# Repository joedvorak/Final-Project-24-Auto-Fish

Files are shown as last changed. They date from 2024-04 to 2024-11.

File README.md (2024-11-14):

# BAE305 Final Project: Automatic Fish Tank Feeder
***BAE305 Final Project***
* Eli Barrow
* Alexis Puckett
* Hannah Markwell

## Summary:

Our BAE305 project is for an aquarium monitoring and feeding system. The system includes an automatic feeder that is on a timer for periods of 6 hours, 12 hours, and 24 hours, and it distributes food directly to the fish in the tank. The feeder uses an auger and stepper motor to push the fish food out of the container, into the fish tank. Our project also includes a mechanism that reads the temperature, displays it, and then turns on a red LED if the temperature falls below a specified point, and a green LED if the temperature is good for the safety of the fish. It also includes a feature that monitors the water level of the fish tank, and this feature turns on an LED to alert low water levels in the tank. Our display system displays the red and green LEDs for both the temperature and water level monitoring systems. It also has two screens, one to show the temperature and water level data, and one to show how much time is left until the next feeding. We used a potentiometer for the user to change the feeding time from 6, 12, and 24 hours. Finally, our display has two potentiometers to control the contrast of the screens. Both the feeder and display mechanical systems are 3D printed.

[Project Video Description: (https://www.youtube.com/shorts/zOCTcbQEuwI)](https://www.youtube.com/shorts/zOCTcbQEuwI)

## Design Description

### Materials:
 
For this project the materials needed are simple electrical components as well as the ability to access a 3D printer to print the larger mechanical parts of the system.
 The electrical components needed are:
 - 2 Arduino Uno Boards with Breadboards
 - Ability to connect the Uno to your computer
 - Approx. 50 wires that're compatible with the Arduino, Breadboard, and components
 - 2 LCD Screens
 - 1 5V DC Stepper Motor (ROHS 28byj-48)
 - 3 Potentiometers
 - 2 Push buttons
 - 2 Green LEDs
 - 2 Red LEDs
 - 1 Float Switch
 - 1 Thermistor
 - 6 1kOhm Resistors 
 - 1 10kOhm Precision Resistor (for thermistor)
 - 1 10 kOhm Resistor

 ### Physical Design: 

The design of the feeding system was a small hopper with an auger in the bottom of it that would be turned by a stepper motor to slowly push the food out of the front of the hopper body. There is a hole that runs from the back of the hopper body to the front of the hopper body where the auger slides into, with a stop being placed on the front side that does not allow the auger to slide all the way through. Below this stop is the funnel shape that the food will slide down into the tank to reach the fish. The base of the auger is specially designed to allow the shaft of the stepper motor to mate into the auger, connecting the two for a smooth rotational motion. The stepper motor came with a screw mounting bracket on each side, we then measured the size of those holes with calipers then created two extrusions on the back side of the hopper that would be used to mount the stepper motor. Then finally for a flush fit of the auger with the back wall of the hopper body some spacers were needed to be put on the shaft to create the proper offset of the stepper motor. The type of food that is normally given to the fish is very small spherical pellets that would almost flow fluidly in a system like this, so this design is what the team moved forward with. There was also a need for the hopper to be mounted to the back glass of the fish tank since there is no spot for the hopper to sit on top of the lid, so the team designed a bracket that mounts to the back glass of the tank for the hopper/feeding system to sit on. The design drawings of the Hopper, Bracket, Auger, and Spacers are shown below, as well as links to the online design file through OnShape, where the .stl files can be exported for 3D printing purposes.

<p align="center">
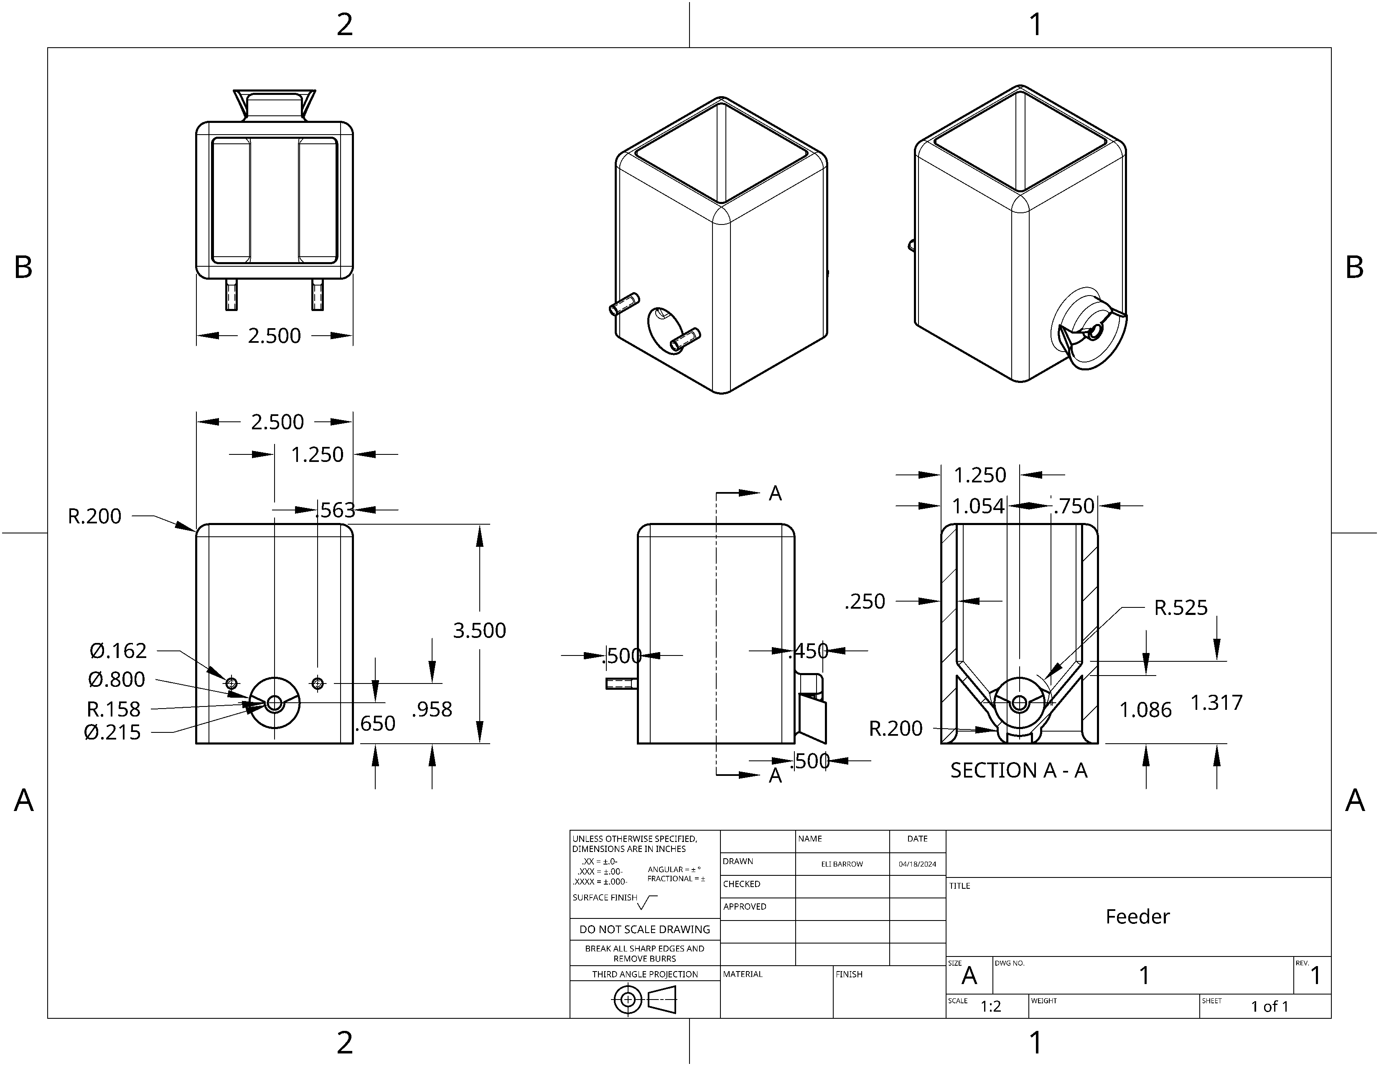
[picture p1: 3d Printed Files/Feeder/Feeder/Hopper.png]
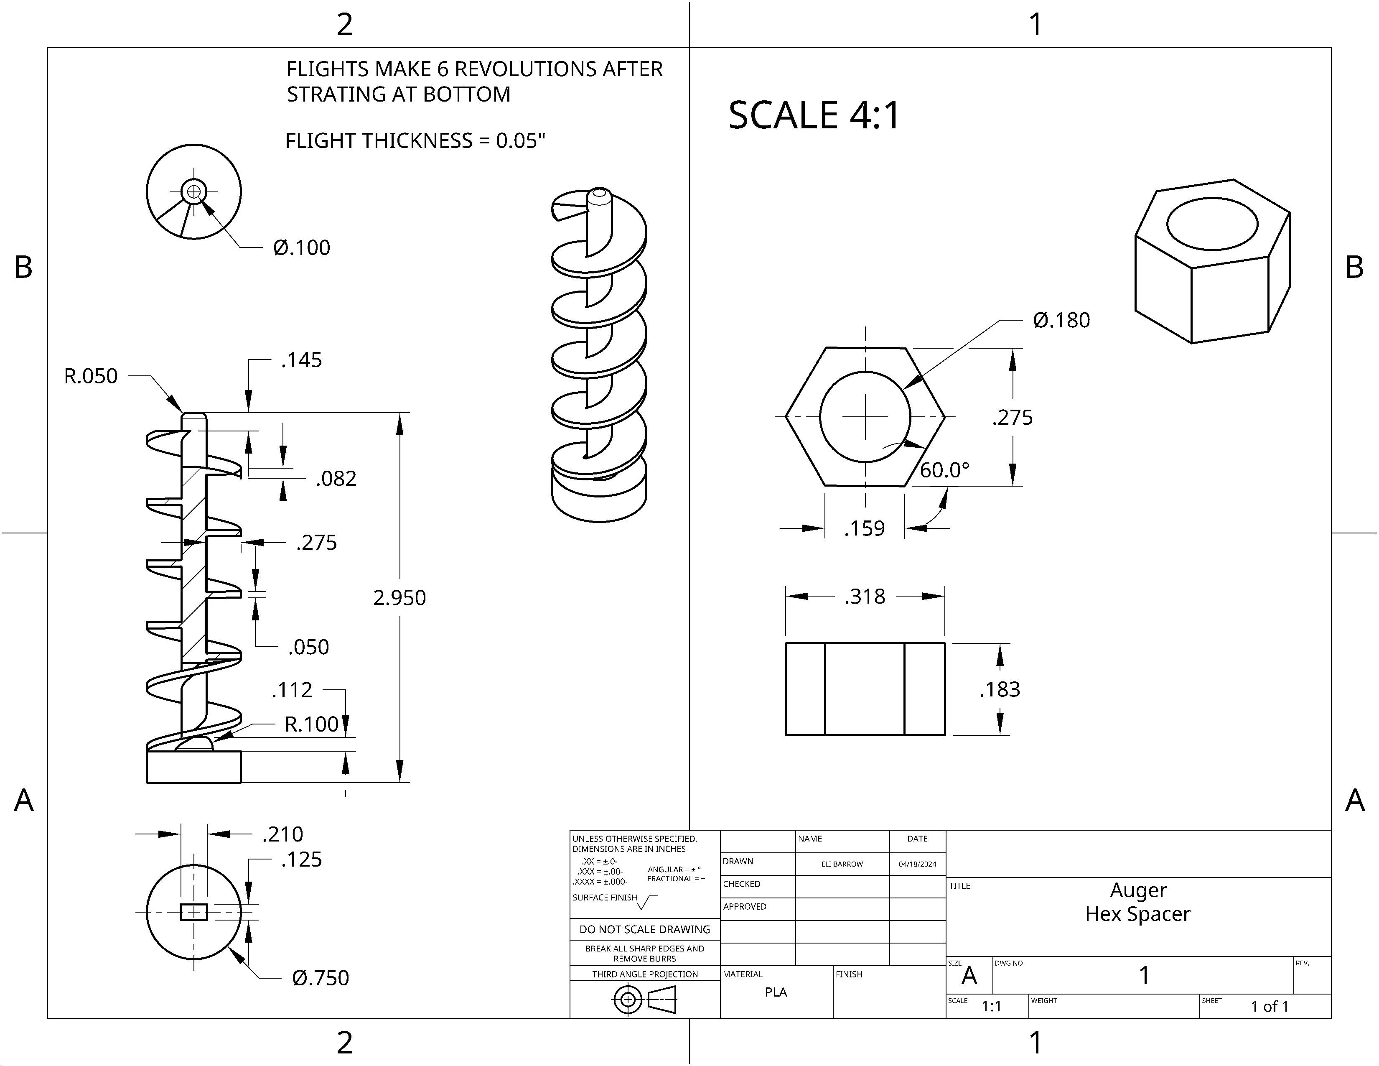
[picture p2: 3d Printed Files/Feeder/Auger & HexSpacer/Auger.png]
  
</p>

<p align="center">
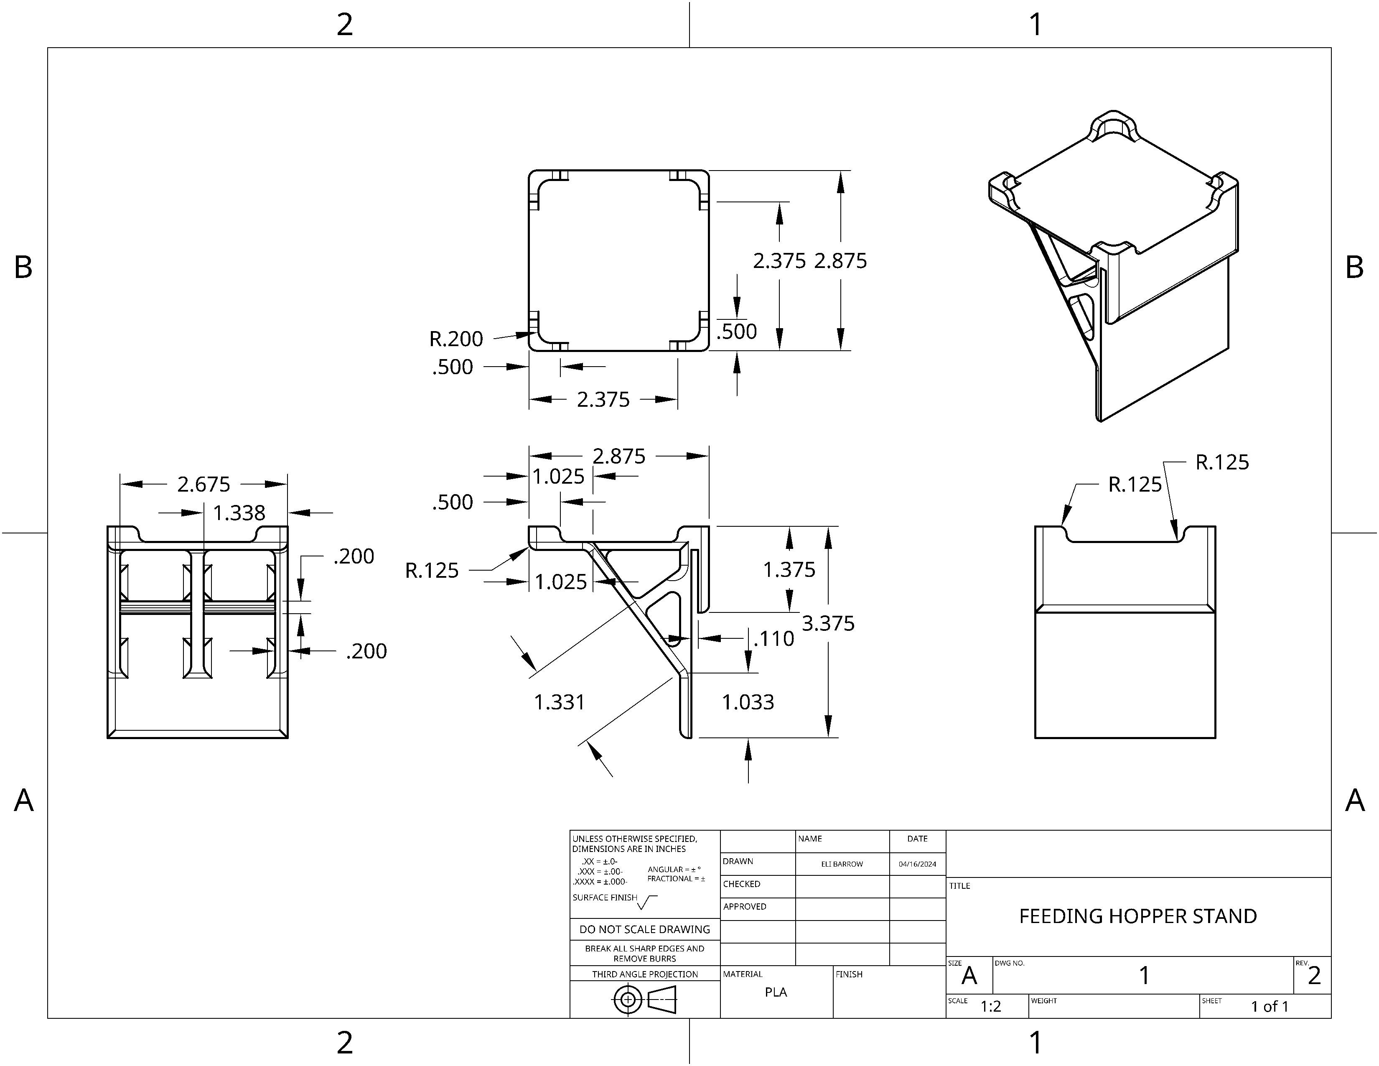
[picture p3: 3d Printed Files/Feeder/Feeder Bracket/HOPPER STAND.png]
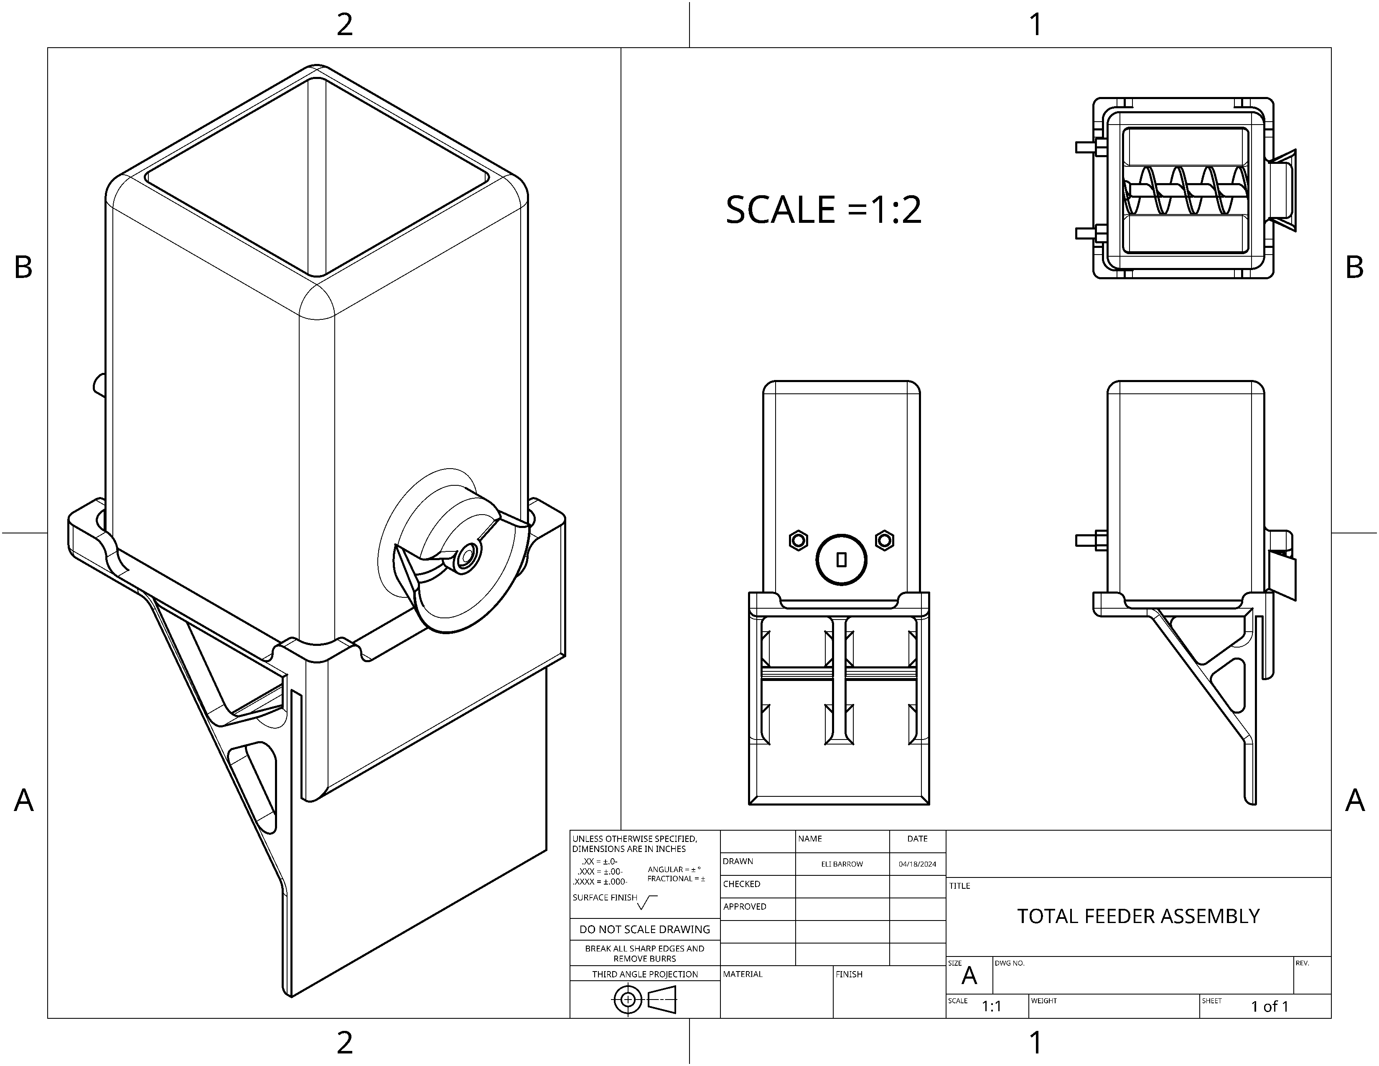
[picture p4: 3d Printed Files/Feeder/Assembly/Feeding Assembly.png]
  
</p>

**Link for Onshape Feeder Files:**
https://cad.onshape.com/documents/4df08dd93363a5b6d688b396/w/b2cb09403d87c3bcf0b51dba/e/0a122a04bef23e0f82b38aa6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

 After designing the Feeding system there was also a need to mount the thermistor and float switch to the back glass of the fish tank alongside the feeder. This only needed a few measurements taken of the float switch diameter and thermistor wire diameter to make a simple bracket, similar to the hopper bracket. The drawing file is shown below and is accompanied with a link to OnShape.

<p align="center">
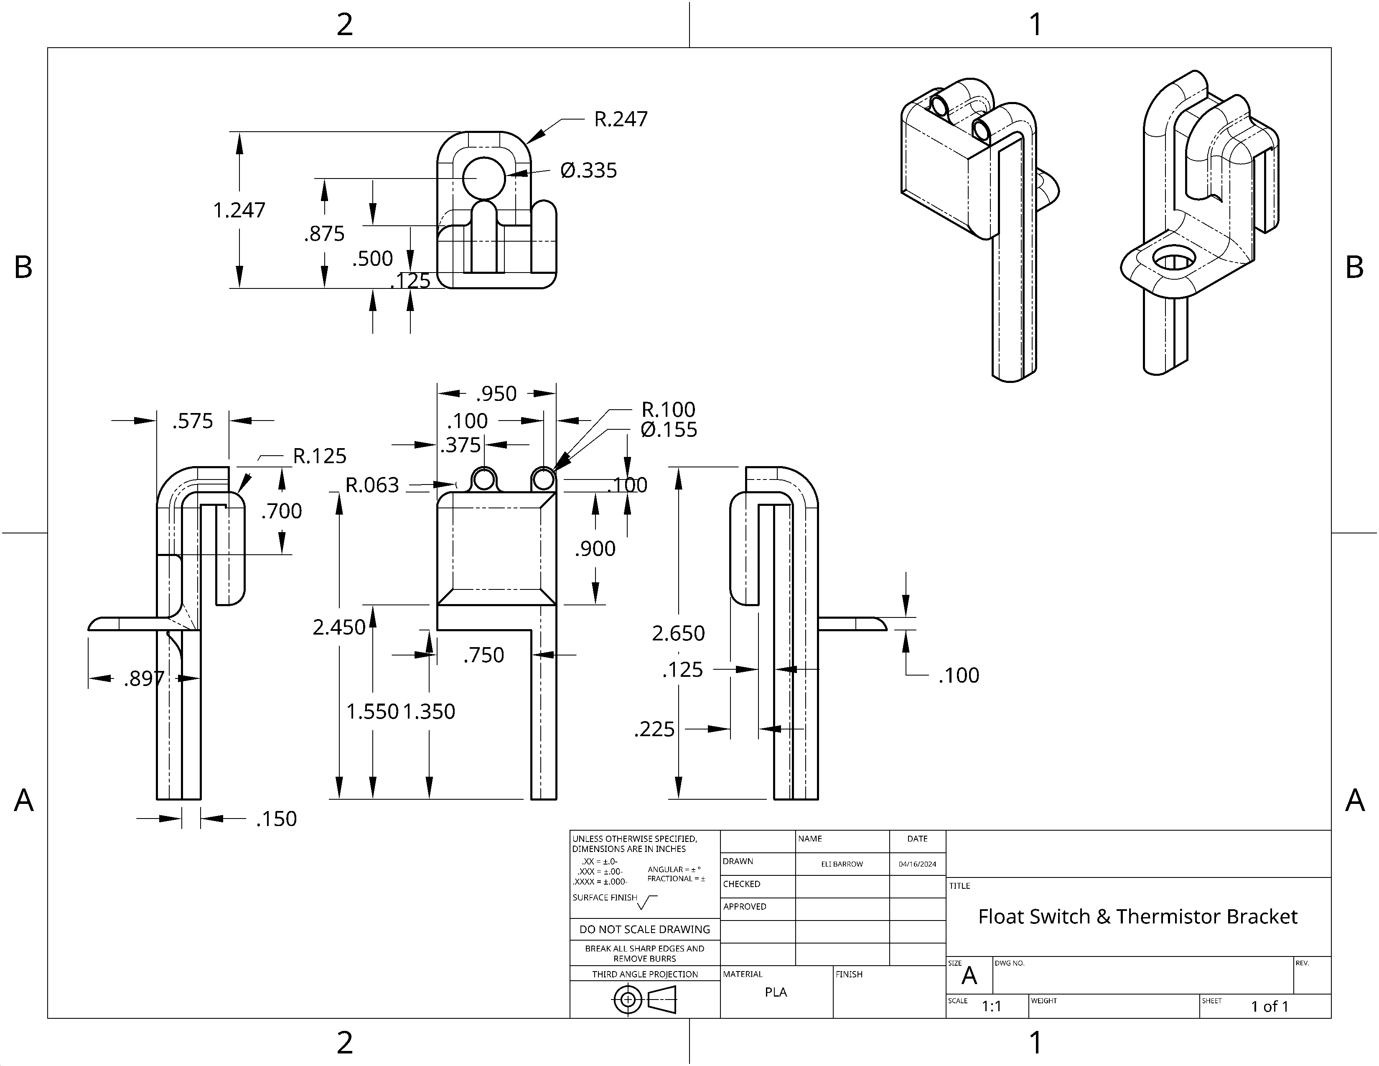
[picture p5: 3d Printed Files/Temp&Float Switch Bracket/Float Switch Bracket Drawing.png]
  
</p>

**Link for Onshape Float Switch & Thermistor Bracket Files:**   
https://cad.onshape.com/documents/ca7b3c8a11bfe362b02dd540/w/57267339f03928a64975b33e/e/b6ae37b48c85a3c1fea425d9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

**Picture of Assembly on Tank with Hopper and Float Switch Bracket:**
<p align="center">
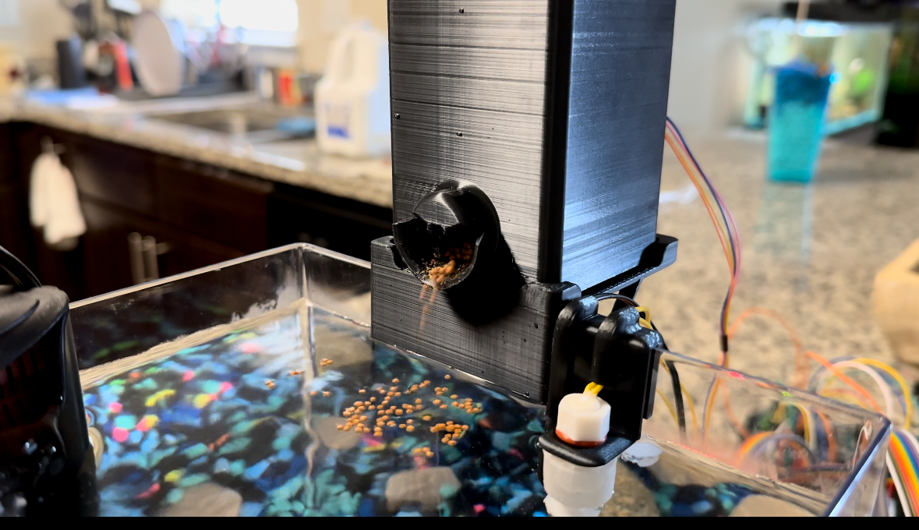
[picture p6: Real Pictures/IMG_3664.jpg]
  
</p>

Once the measurement tools and feeding systems were designed the only piece remaining was a panel for the user to control the system with. The group had previously put together the circuits for the project and had previously known that we need positions for a selecting button, reset button, a potentiometer for choosing the time interval, spaces for 4 LEDs, 2 spaces for LCD screens and finally 2 more potentiometers for controlling the contrast of the screens. The group measured the dimensions of the electrical components with calipers and put together the following control panel that will be used to control the system. The control panel also was in need of a back plate that could be removed that would allow someone to connect wires to the electrical components. There was also a need for braces that would keep the LCD screens in place to assure that they would be flush with the front surface of the control panel for a smooth exterior look. The tolerances were tight enough for the smaller components, so they did not need braces to be held into place. The drawing file of the control panel, back plate, internal braces, and assembly drawing is shown below and is accompanied with a link to OnShape.

<p align="center">
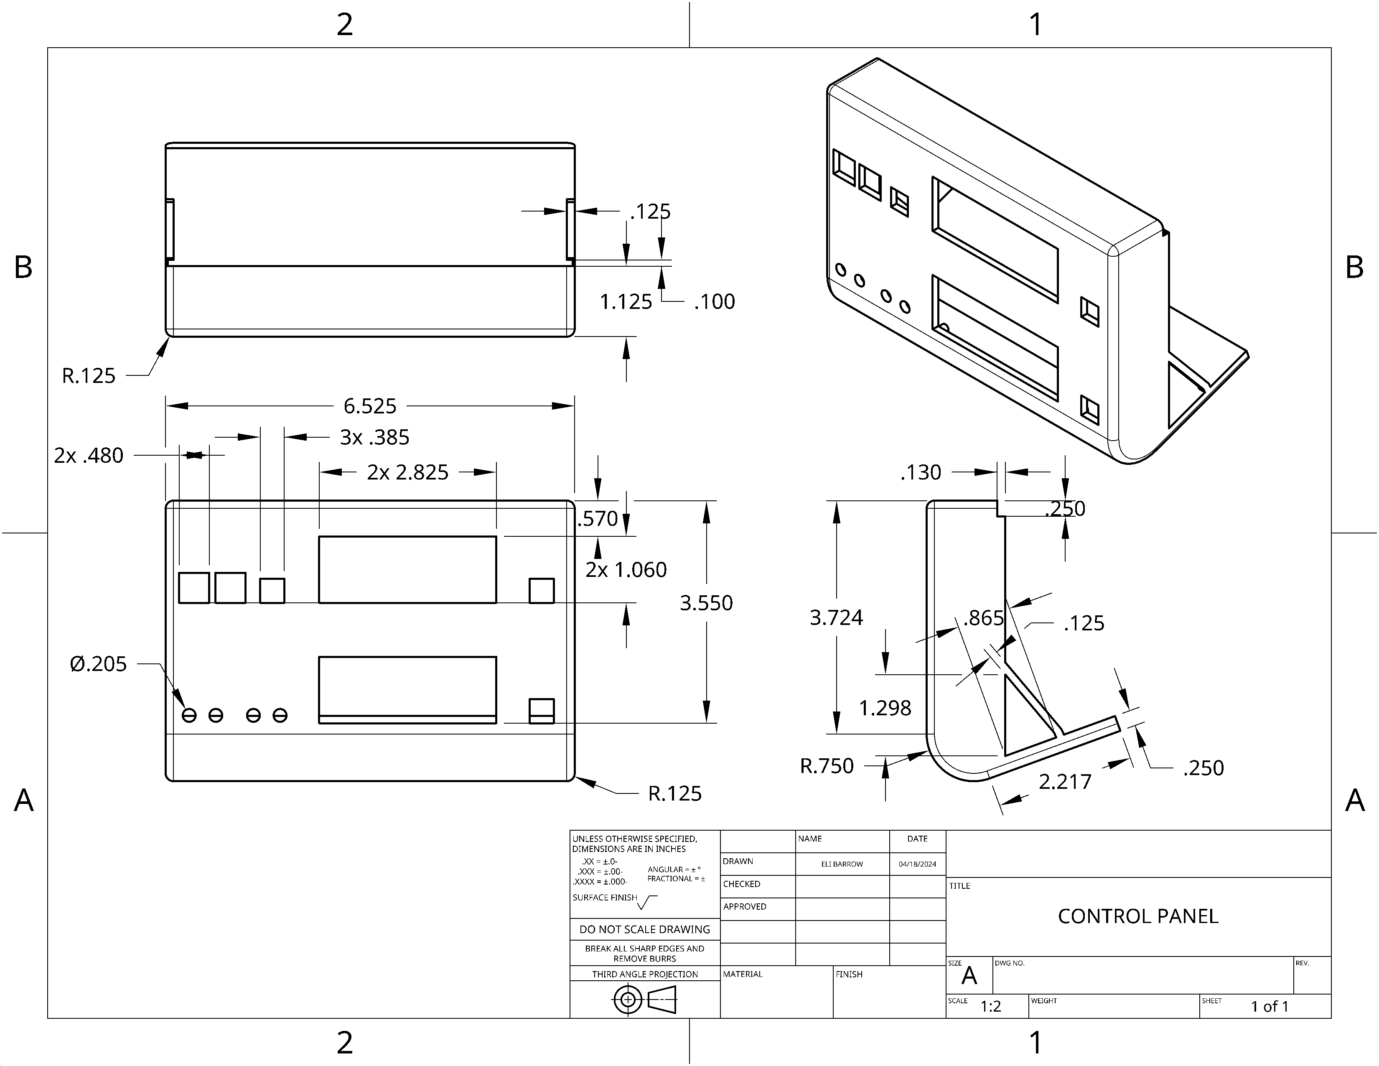
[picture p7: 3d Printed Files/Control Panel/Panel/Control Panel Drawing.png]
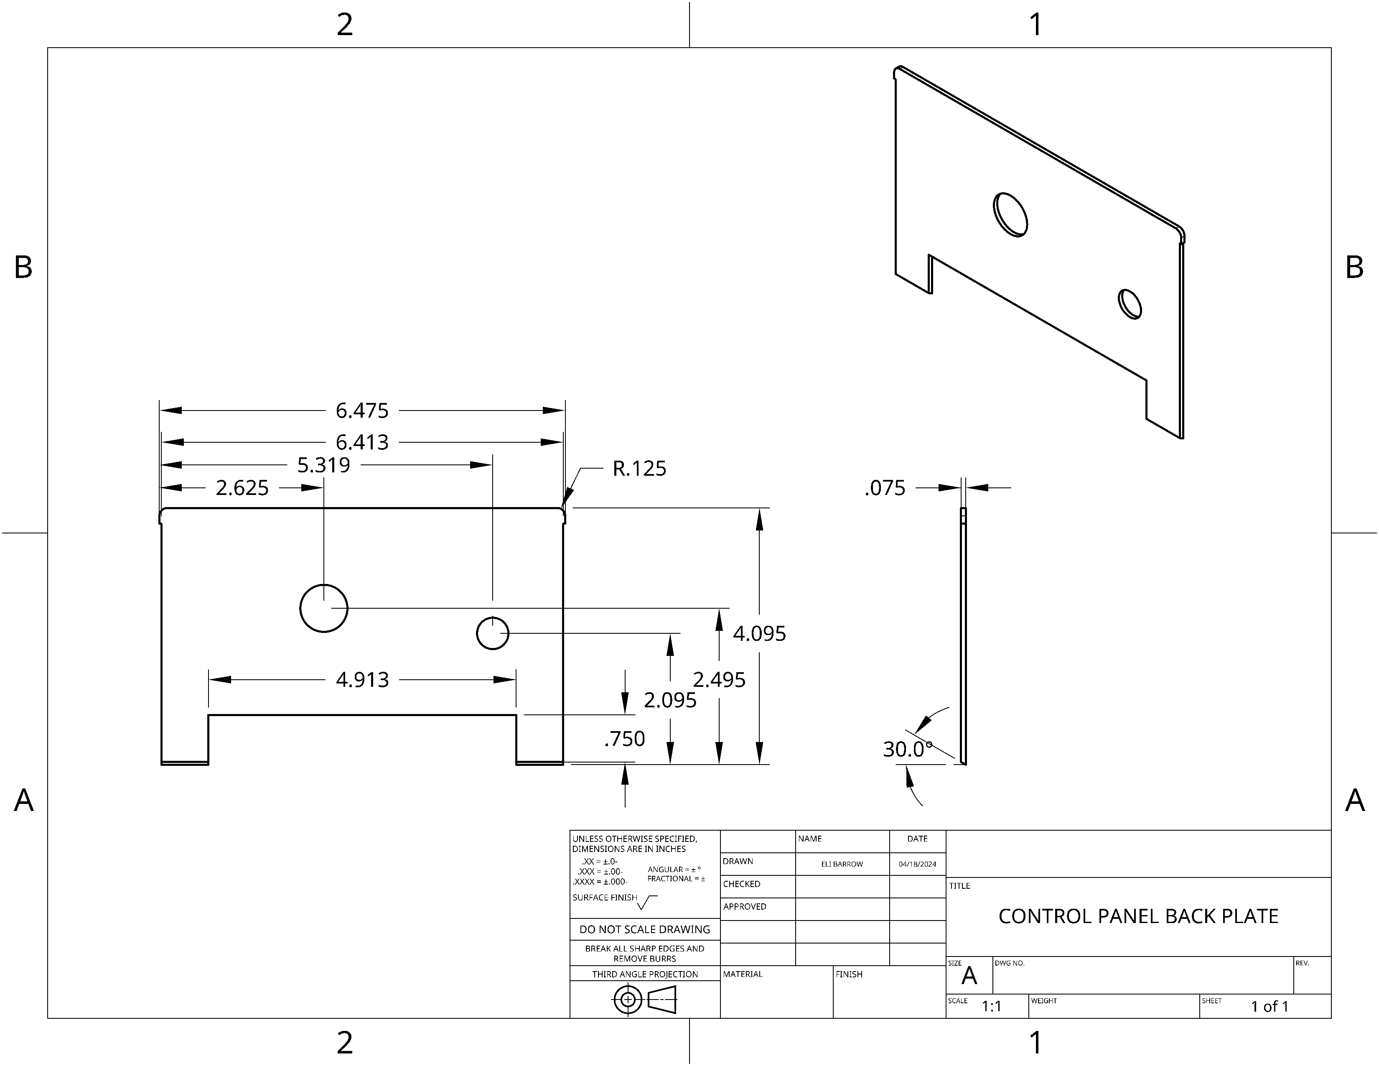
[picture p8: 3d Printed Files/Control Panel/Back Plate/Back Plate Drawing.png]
  
</p>

<p align="center">
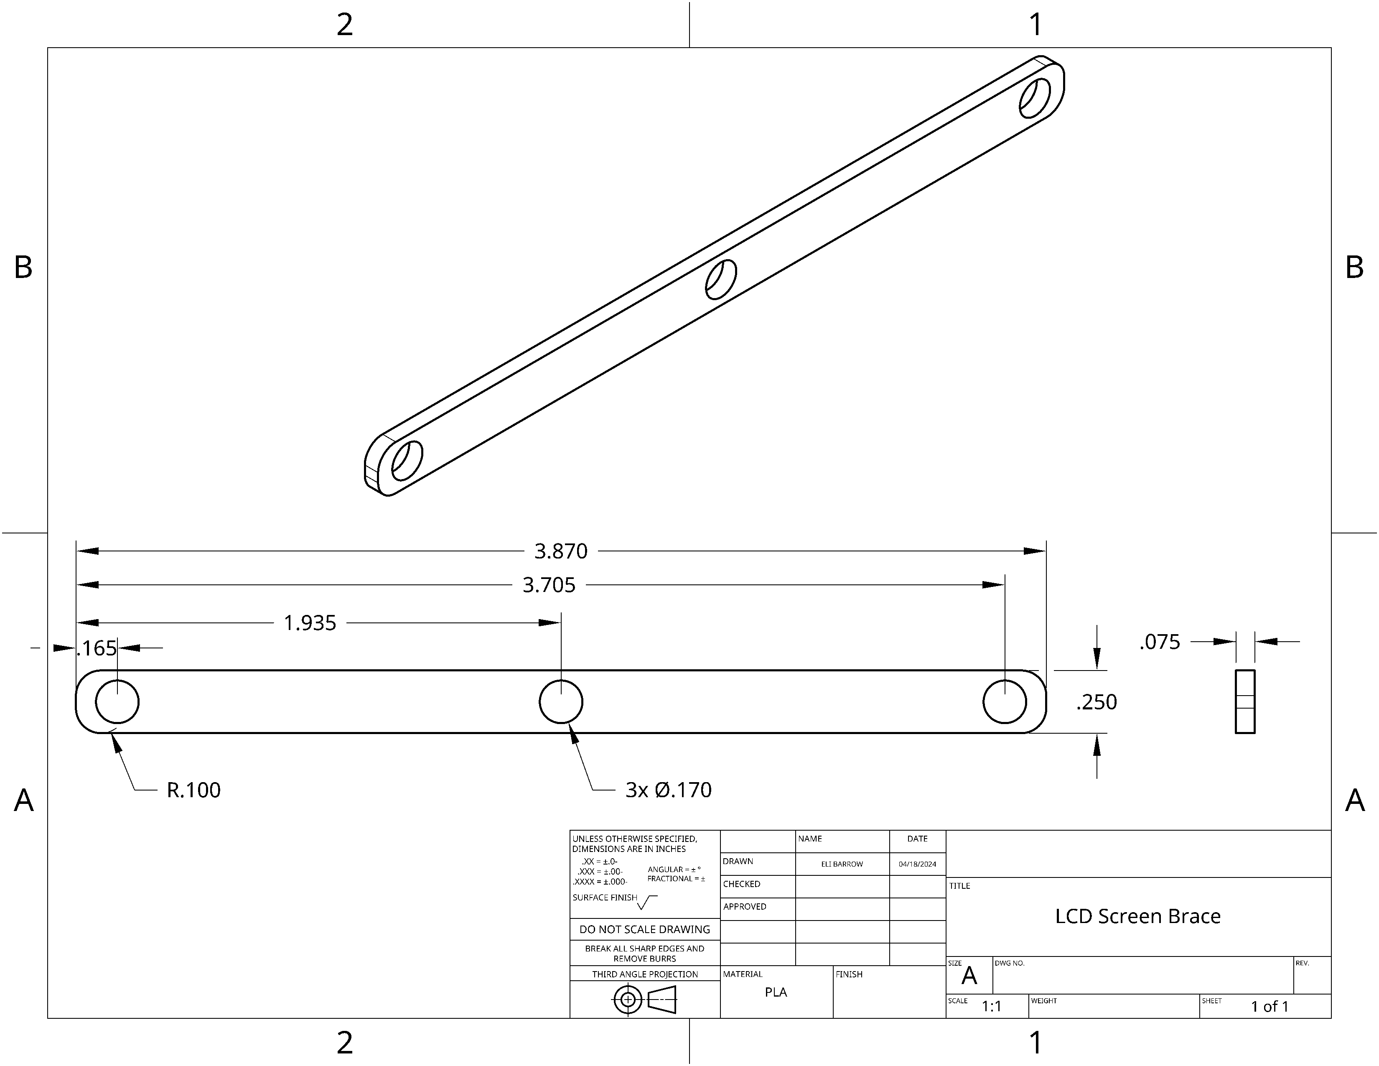
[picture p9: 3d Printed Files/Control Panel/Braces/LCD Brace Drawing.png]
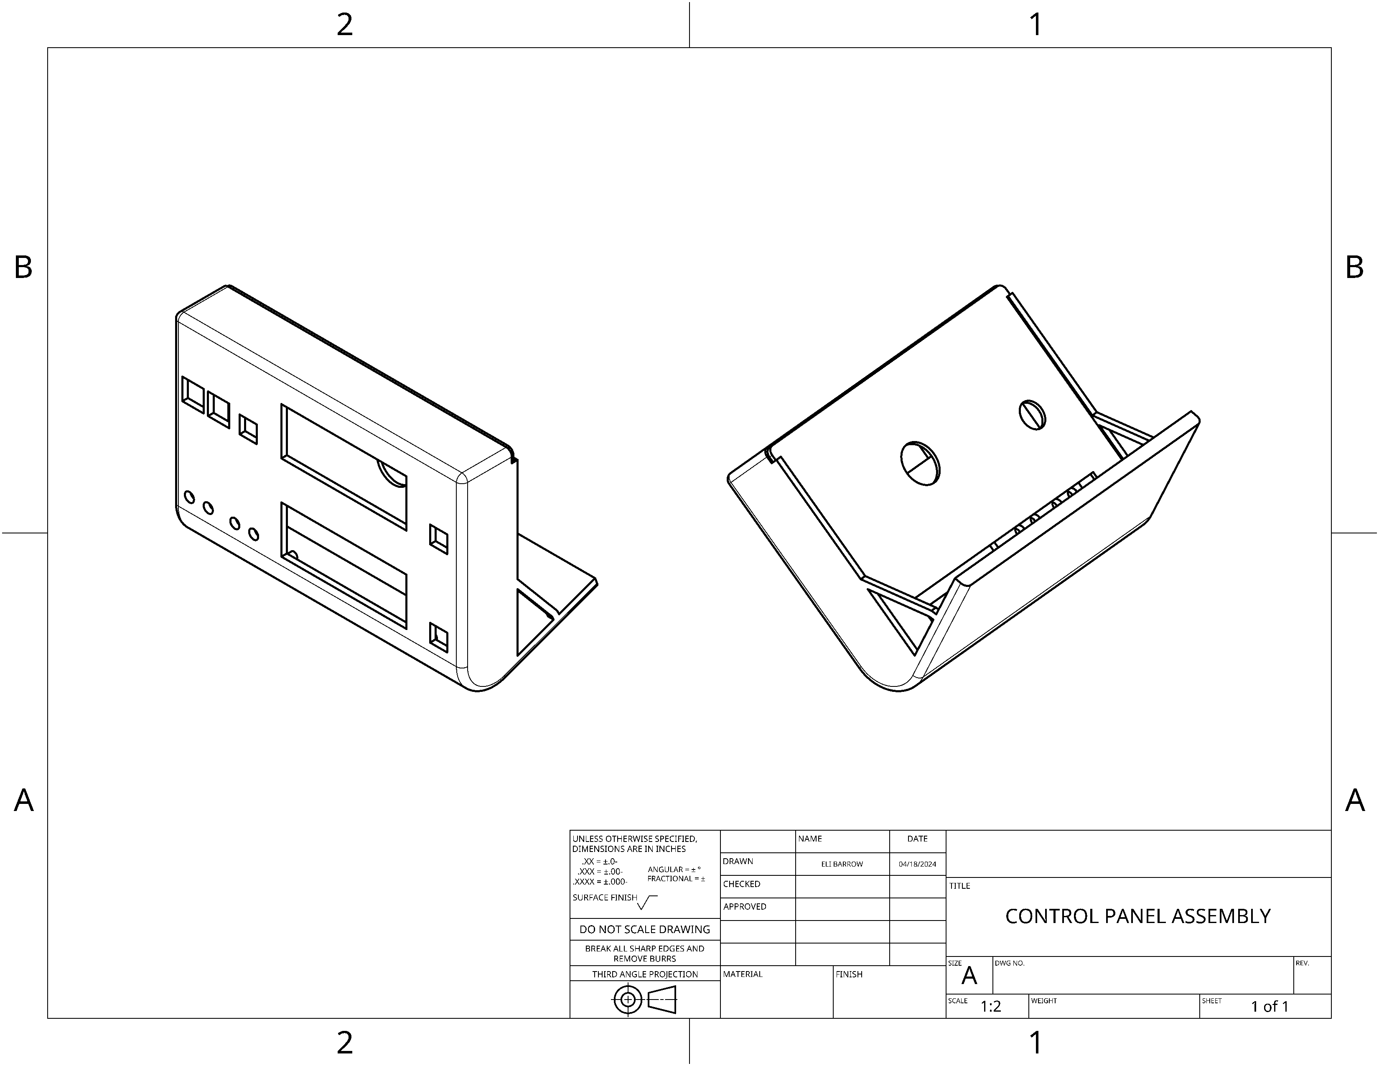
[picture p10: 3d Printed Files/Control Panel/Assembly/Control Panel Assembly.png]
  
</p>

**Link for Onshape Control Panel Files:**   
https://cad.onshape.com/documents/7f8683062ff1f39808deca4c/w/c8f5f551fcbae8743f684af5/e/5d18dd19f17cefe8056f8dae    

**Picture of Final Control Panel:**
<p align="center">
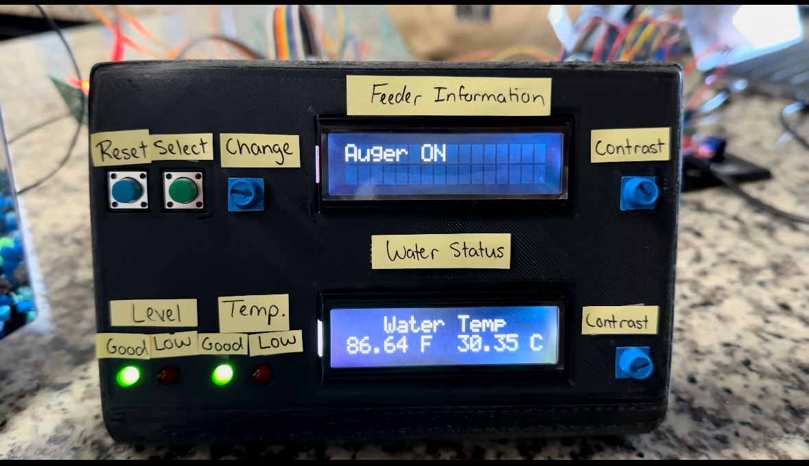
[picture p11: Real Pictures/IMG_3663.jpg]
  
</p>

 ### Circuits:
For our project, we used two seperate Arduinos to run everything. One Arduino controlled the temperature and water level system and the other controlled the feeder system. These Arduinos are not in communication with eachother. We thought this would be best in order to simplify the code, and if one system failed to work, the other one could still work.

<p align="center">
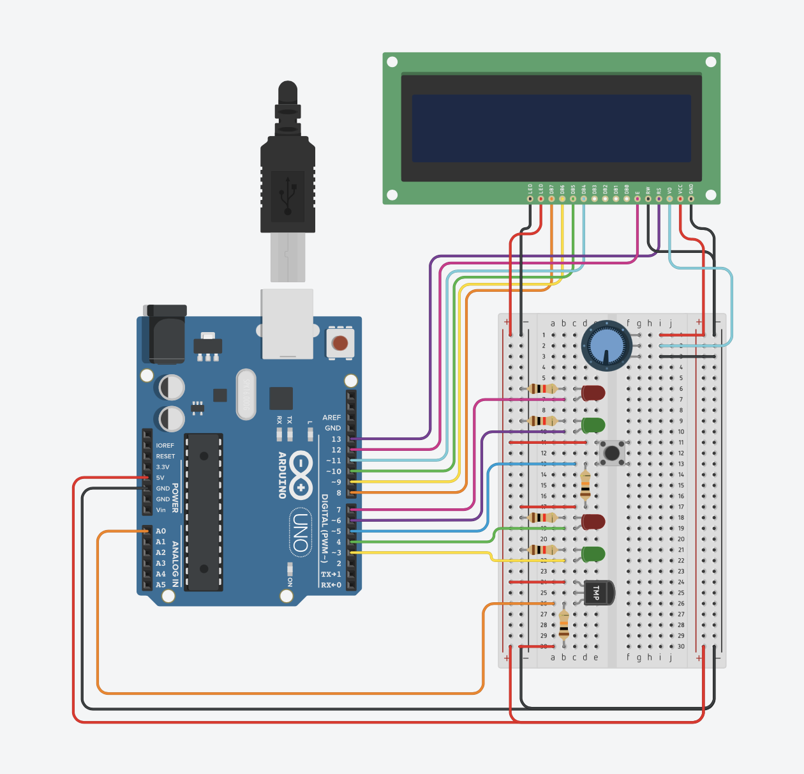
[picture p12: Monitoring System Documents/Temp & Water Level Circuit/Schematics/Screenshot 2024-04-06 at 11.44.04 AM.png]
  
</p>

**NOTE:** The push button on this schematic is representing the float switch. The software used did not provide a float switch so this was best option. The resistor connected to the thermistor is the 10k precision resistor.

The above schematic is for the temperature and water level sensor system. It uses an Arduino Uno Board, a common breadboard, a 10kOhm precision resistor, four 1kOhm resistor, two red LEDs, two green LEDs, a thermistor, a potentiometer, a float switch, and a LCD screen. The potentiometer is to control the contrast of the LCD screen. This screen displays both the temperature and the waterlevel information.

<p align="center">
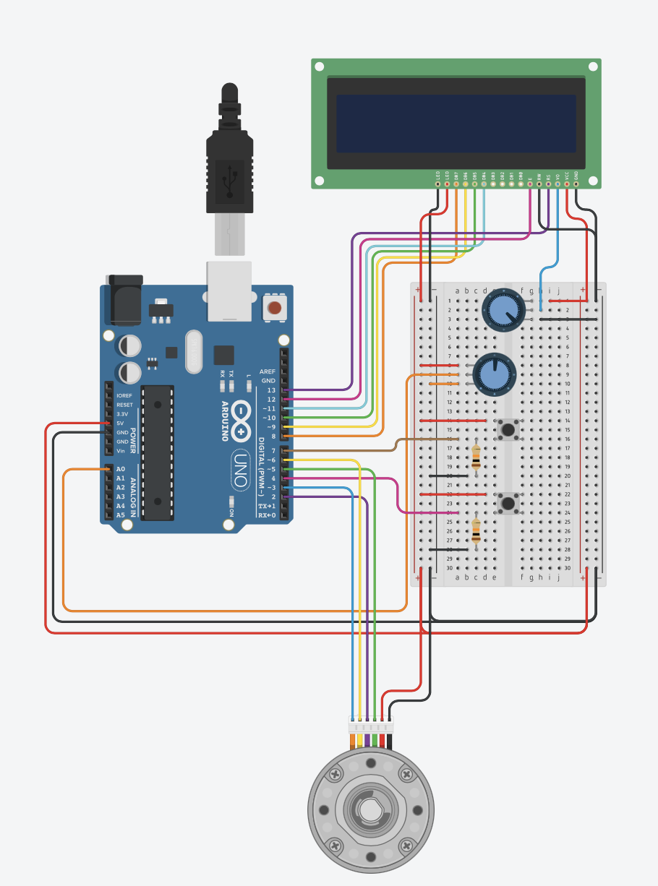
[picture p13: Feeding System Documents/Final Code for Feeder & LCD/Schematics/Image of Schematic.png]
  
</p>

The above schematic is for the temperature and water level sensor system. It uses an Arduino Uno Board, a common breadboard, a 10kOhm precision resistor, four 1kOhm resistor, two red LEDs, two green LEDs, a thermistor, a potentiometer, a float switch, and a LCD screen. The potentiometer is to control the contrast of the LCD screen. This screen displays both the temperature and the water level information.

 ### Code: ###

 Sine the code for our project is a few hundred lines long, it will be included in links below to another section in this repository. Both of these links are the .INO files that can be downloaded and ran in the arduino software.(Both sets of code are equipped with comments describing the purpose of each line)   
 **Link for Feeder Code:**   
https://github.com/elibarrow/Final-Project/blob/main/Feeding%20System%20Documents/Final%20Code%20for%20Feeder%20%26%20LCD/Code/DC.LCD.ino   

 **Link for Monitoring Code:**   
 https://github.com/elibarrow/Final-Project/blob/main/Monitoring%20System%20Documents/Temp%20%26%20Water%20Level%20Circuit/Code/Temp.FloatSwitch.ino

 ### Assembly:

 The assembly part of this project was mostly simple. We had already created the schematics of the wiring and had previously uploaded the code to the Arduino boards. The 3d printed parts had already been confirmed to fit properly together, so there was no worry associated with that aspect. One minor issue that we ran into while assembly the final product was that we needed a few longer wires to connect everything together because of the size of the two Arduino boards, but this was a simple fix of just ordering some longer wires. The final minor issue that we ran into was the wires not staying put into the breadboard or staying attached to the pins on the button, we just made sure that everything was properly connected before testing out project. If this problem became serious enough, we could have soldered the connections together, which would have completely gotten rid of this issue.

 **Picture of Finished Project on the Fish Tank:**
<p align="center">
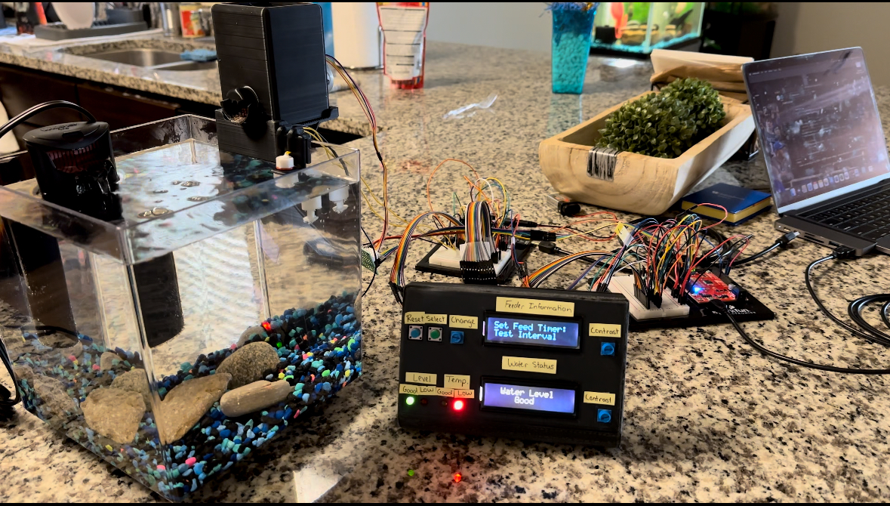
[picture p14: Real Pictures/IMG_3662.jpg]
  
</p>

## Test Description
 The project that we created should be somewhat simple to test. Beginning with the control panel user inputs, by turning the potentiometer that is to the left of the top LCD screen it will change the time interval for the next scheduled feeding. There will be options for a 6 hr., 12 hr., 24 hr., & a Test interval. To choose an interval the green select button needs to be pressed while the desired interval is on the screen. As assumed the 6 hr., 12 hr., and 24 hr. intervals will begin with a feeding of approximately 15 seconds, the screen will show "Auger On" during this period. Afterwards the timer will begin to count down for the selected interval, however for testing purposes, the Test option is only set to a 10 second timer. This makes the feeding almost constant, running a new 15 second feeding every 10 seconds, which allows for the user to assure that the auger is properly turning and dispensing food before setting the longer timer. However, if something happens and you need to reset the feeding system you can press the reset button, but only while the countdown is happening on the screen. The reset button has no effect while the auger is dispensing food. After pressing the reset button, you may choose a new feeding cycle and start the process over again.    
The other part of the system to look at will be the monitoring system, this system has no user inputs and only displays the information that has been gathered by the float switch and thermistor. There are a green and red LED for both the temperature and water level. As the temperature reaches the desired amount that has been set in the code the green light will be illuminated, but if the temperature exceeds or drops below that interval the red light will turn on. Likewise, as the float switch is down, the red light will be illuminated showing the water level is low, but if it is up the green light will be on signaling good water levels. Both of these inputs are also displayed on the LCD screen. The temperature is given in F and C, if these values are extremely high or low you might want to assure the thermistor is properly connected to the breadboard. Similarly, the LCD screen will then switch to give a status update on the water level, if the water is low, it will tell the user to put more water in the tank, if the water is at a good level it will say "Water level good". The LCD screen flips back and forth between the temperature and the water level about every 10 seconds, which also means the LEDs update every 10 seconds.   
A good testing procedure would be to let the system run for a few hours to make sure that everything is running properly for an extended period of time.

## Design Decision Discussion

The design of this system was purely driven by one of the group member's experiences with being away from a fish tank at their home for an extended period of time and not being able to feed their fish. After the group began considering this, the others then added some other features to add to the system, rather than just making a fish feeder. This ultimately led the group to pursue a design that included an automatic feeder, water temperature monitor and a water level monitor. The mechanical design of the project was strictly driven by the constraints that were presented by the fish tank that it was being designed for. The fish tank did not have a viable place for a feeder to sit on the lid, but there is an opening in the backside of the lid that would allow for the feeder to be attached to the glass, as well as the addition of a temperature sensor and water level sensor. Since this project had a budget of $0, we chose materials that were very cheap and used online software that is free to use, such as OnShape and TinkerCAD.

## Results

The capabilities of the entire project are fully described in the Test description part of this report. There is not any outside equipment that is needed to test the system, but you could run the system for a few hours to make sure the timing is working properly, and nothing will go wrong. This design is specific to only to fish tank it was designed for, but it could be integrated into other fish tanks or systems by changing the type of mounting brackets. The mounting brackets made were specific to the targeted fish tank and it is highly unlikely that any other tank will have the same dimensions. After conducting numerous hours of testing our system works very fluidly, the only noticeable flaw is the countdown timer stays on certain numbers because it only updates once every second, if it were to update more often this would not be an issue. For example, when it takes a reading at 4.99 seconds it displays 4 seconds, but when it may jump the gun and reads at 4.01 seconds, it still displays 4 seconds for the next duration. Although the displaying of this may be a little off the true internal timer is accurate and will work as described. The limitations of this system will be if it is in a moist environment, some of the electrical components may end up rusting or not working properly. There should be some sort of water protection over the Arduinos to make sure this is not an issue. This system is incapable of knowing how much food to dispense at one time depending on volume, it dispenses based on a time interval. The same volume of food being dispensed every time is highly unlikely.   
 When the group began doing final testing on the project the first test was to let it run through each cycle completely to make sure it worked properly, and after each one of those tests, no flaws were found. We also tried pressing the reset and select buttons at random times when they were not supposed to do anything during the cycle and that as well did not bring upon any problems. We did not do any moisture level testing or water resistance tests because we did not want to ruin our project and that is to certainly bring issues. Overall, for what the system is built to do, it seems to be very robust and can do the tasks effectively.

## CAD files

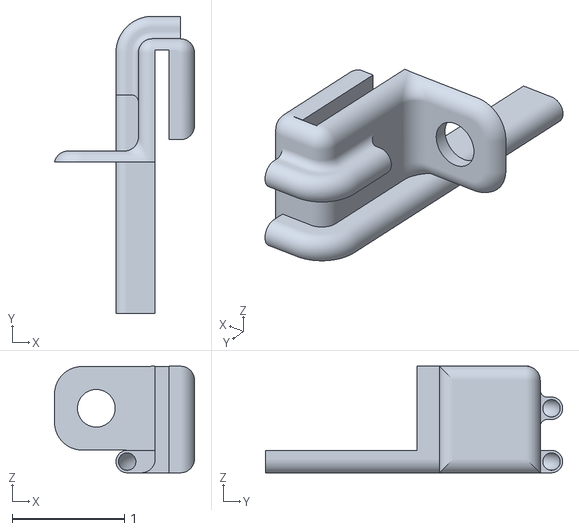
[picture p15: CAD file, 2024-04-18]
3d Printed Files/Temp&Float Switch Bracket/Float Switch Bracket.stl
1.25 x 2.65 x 0.95

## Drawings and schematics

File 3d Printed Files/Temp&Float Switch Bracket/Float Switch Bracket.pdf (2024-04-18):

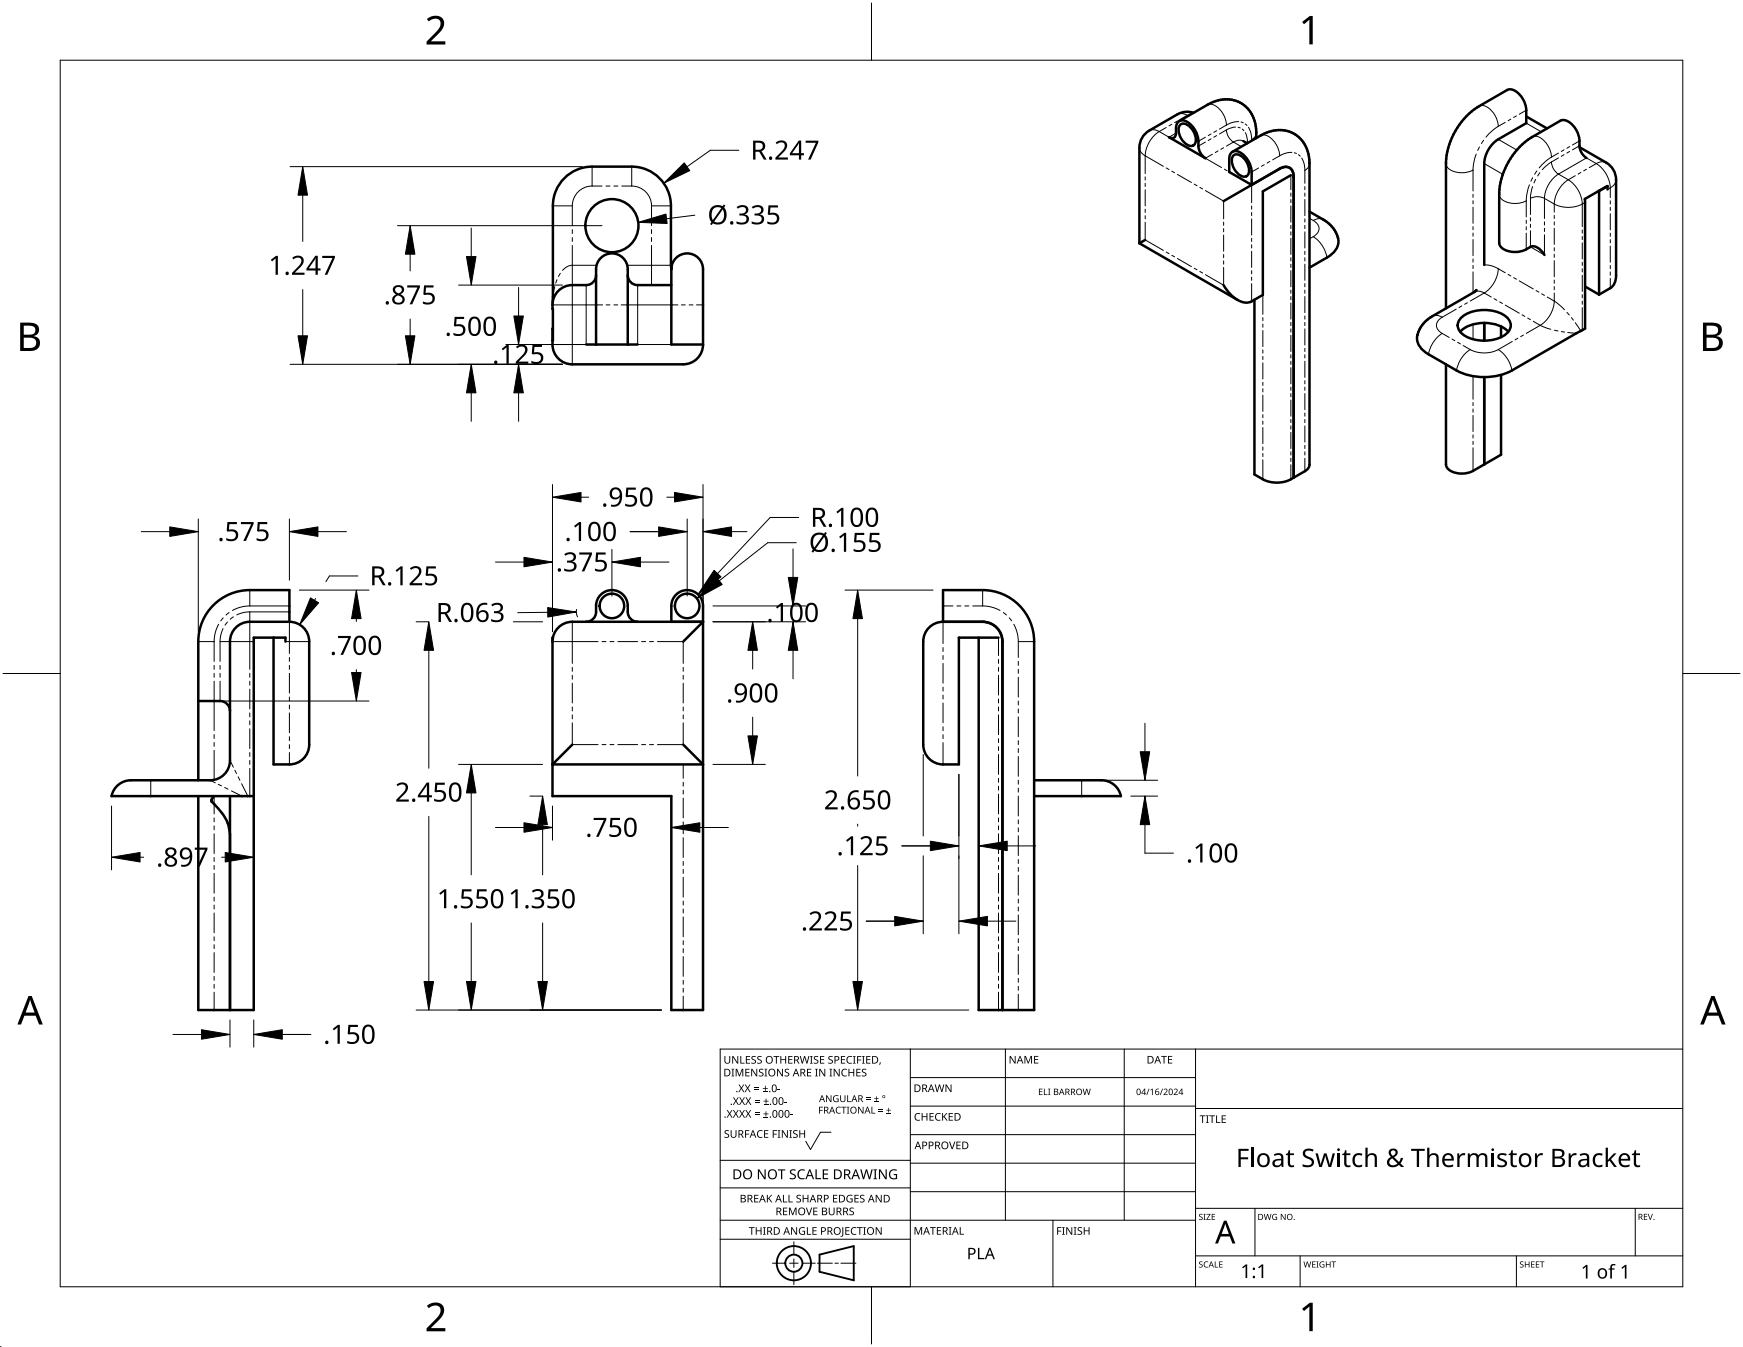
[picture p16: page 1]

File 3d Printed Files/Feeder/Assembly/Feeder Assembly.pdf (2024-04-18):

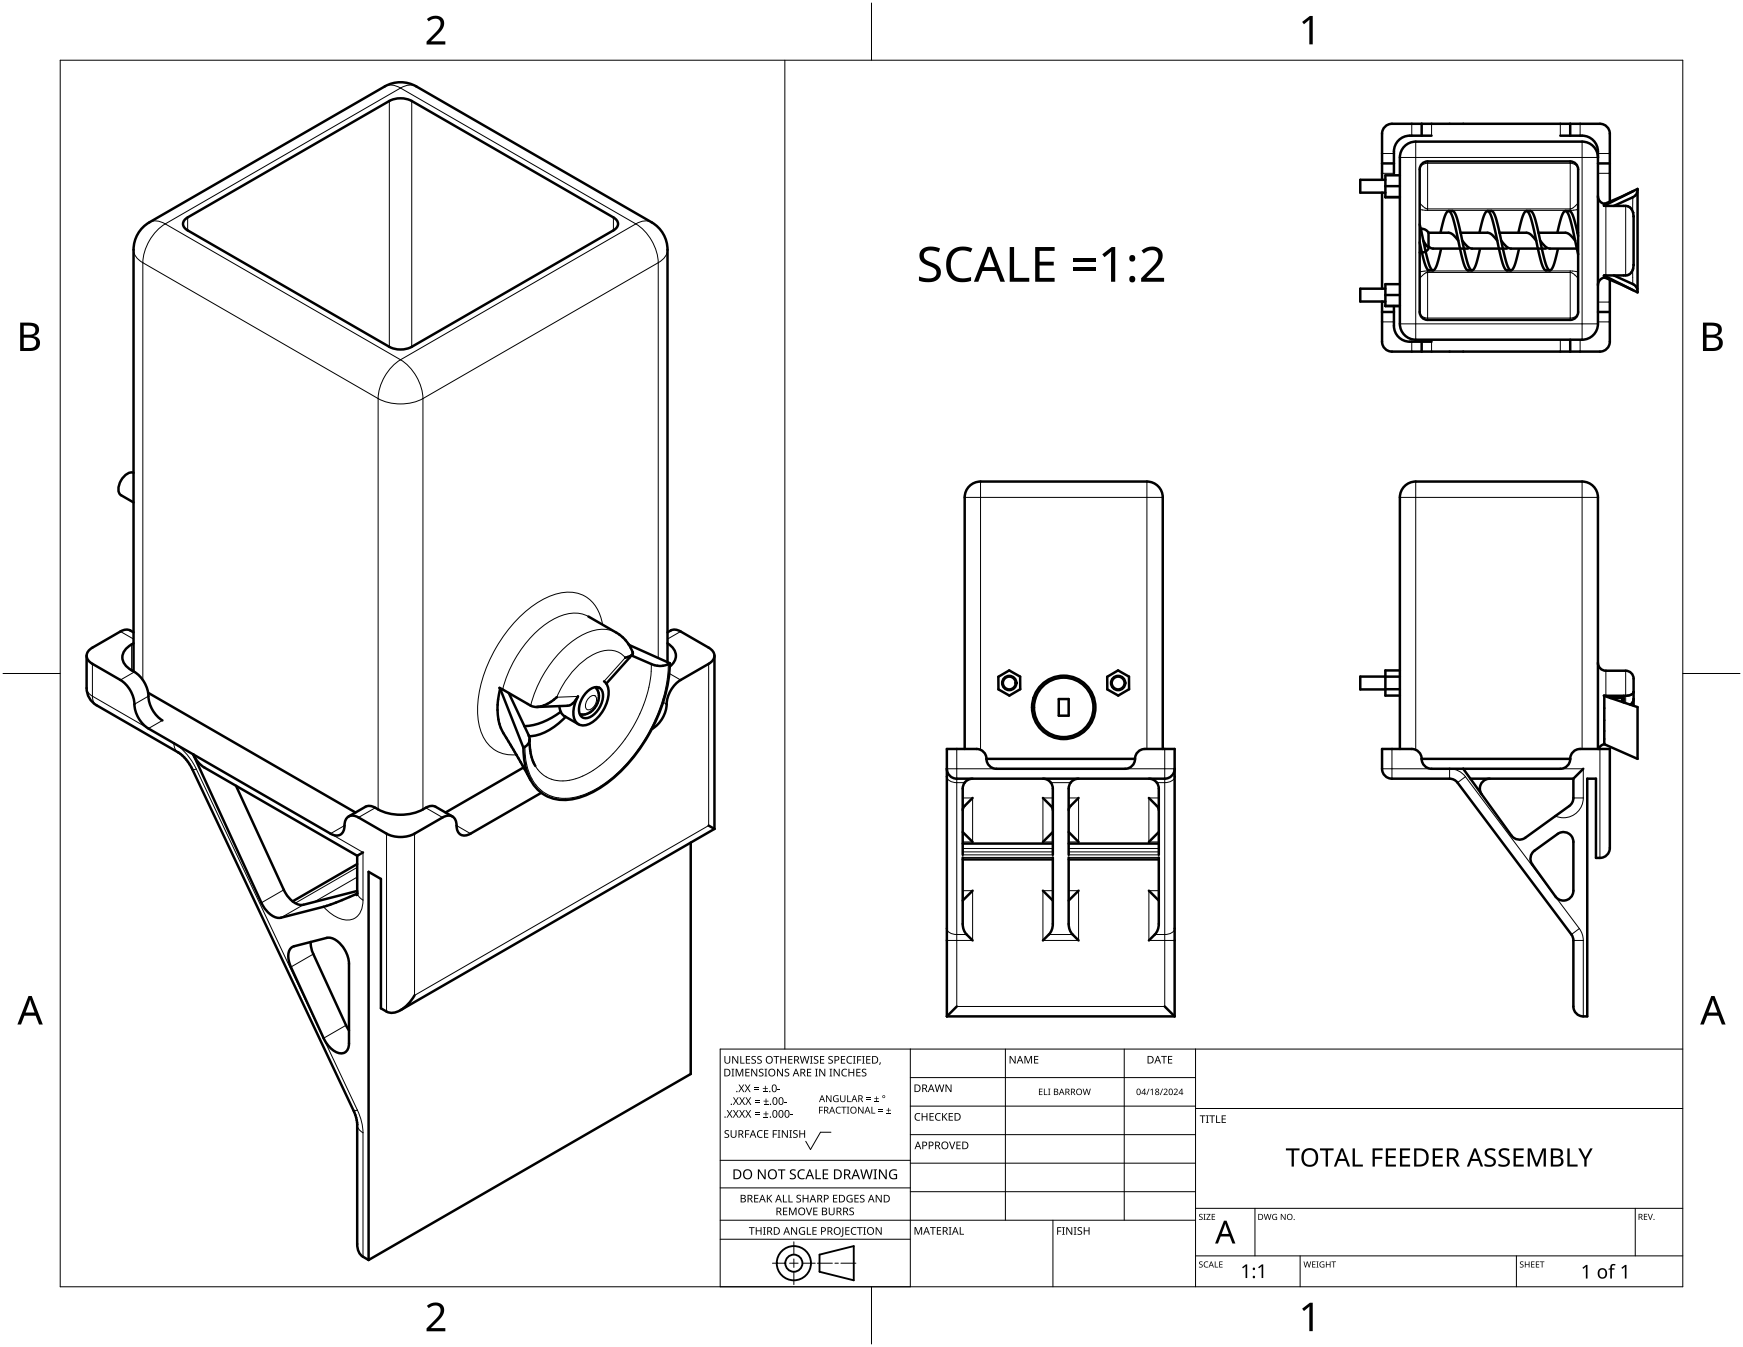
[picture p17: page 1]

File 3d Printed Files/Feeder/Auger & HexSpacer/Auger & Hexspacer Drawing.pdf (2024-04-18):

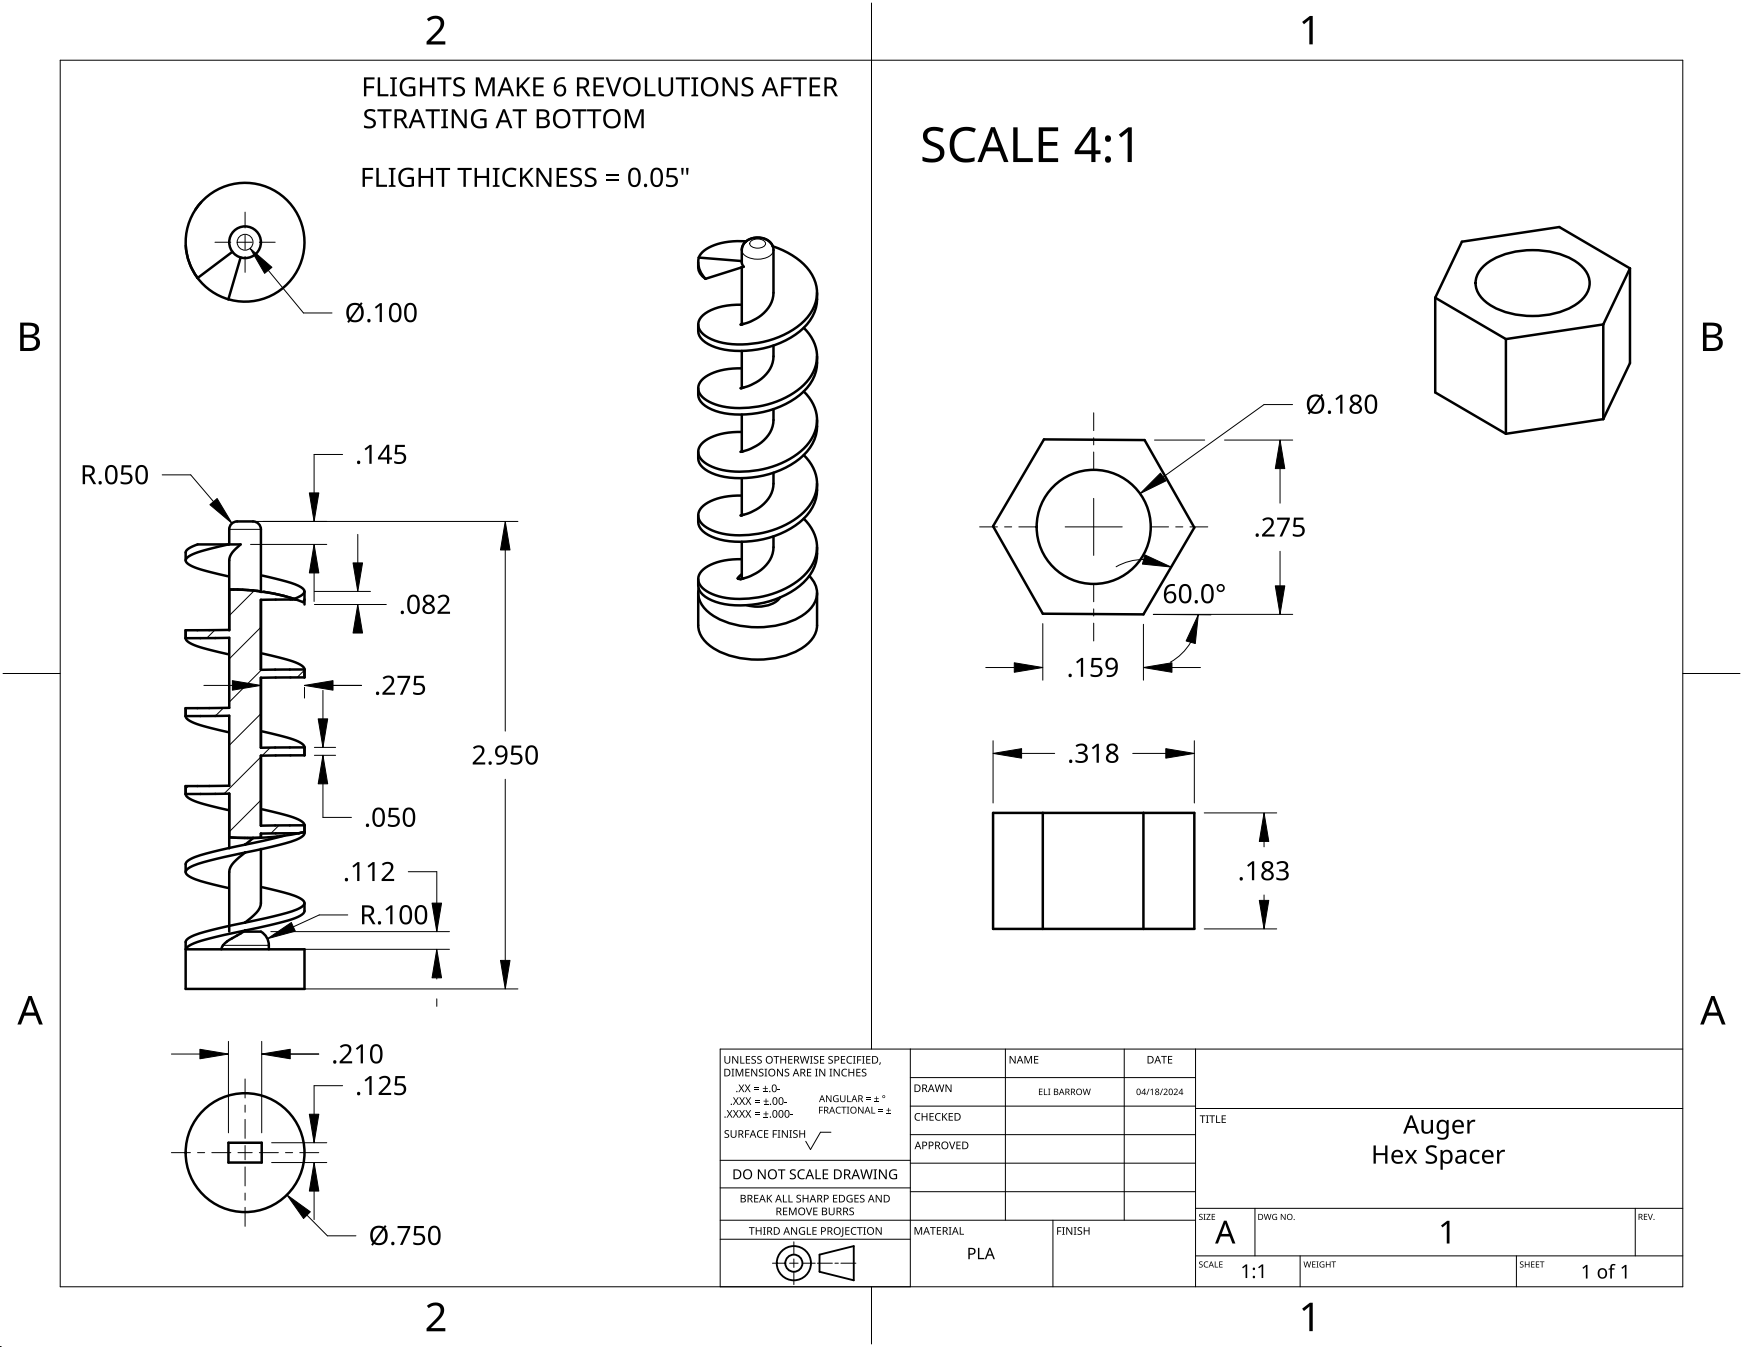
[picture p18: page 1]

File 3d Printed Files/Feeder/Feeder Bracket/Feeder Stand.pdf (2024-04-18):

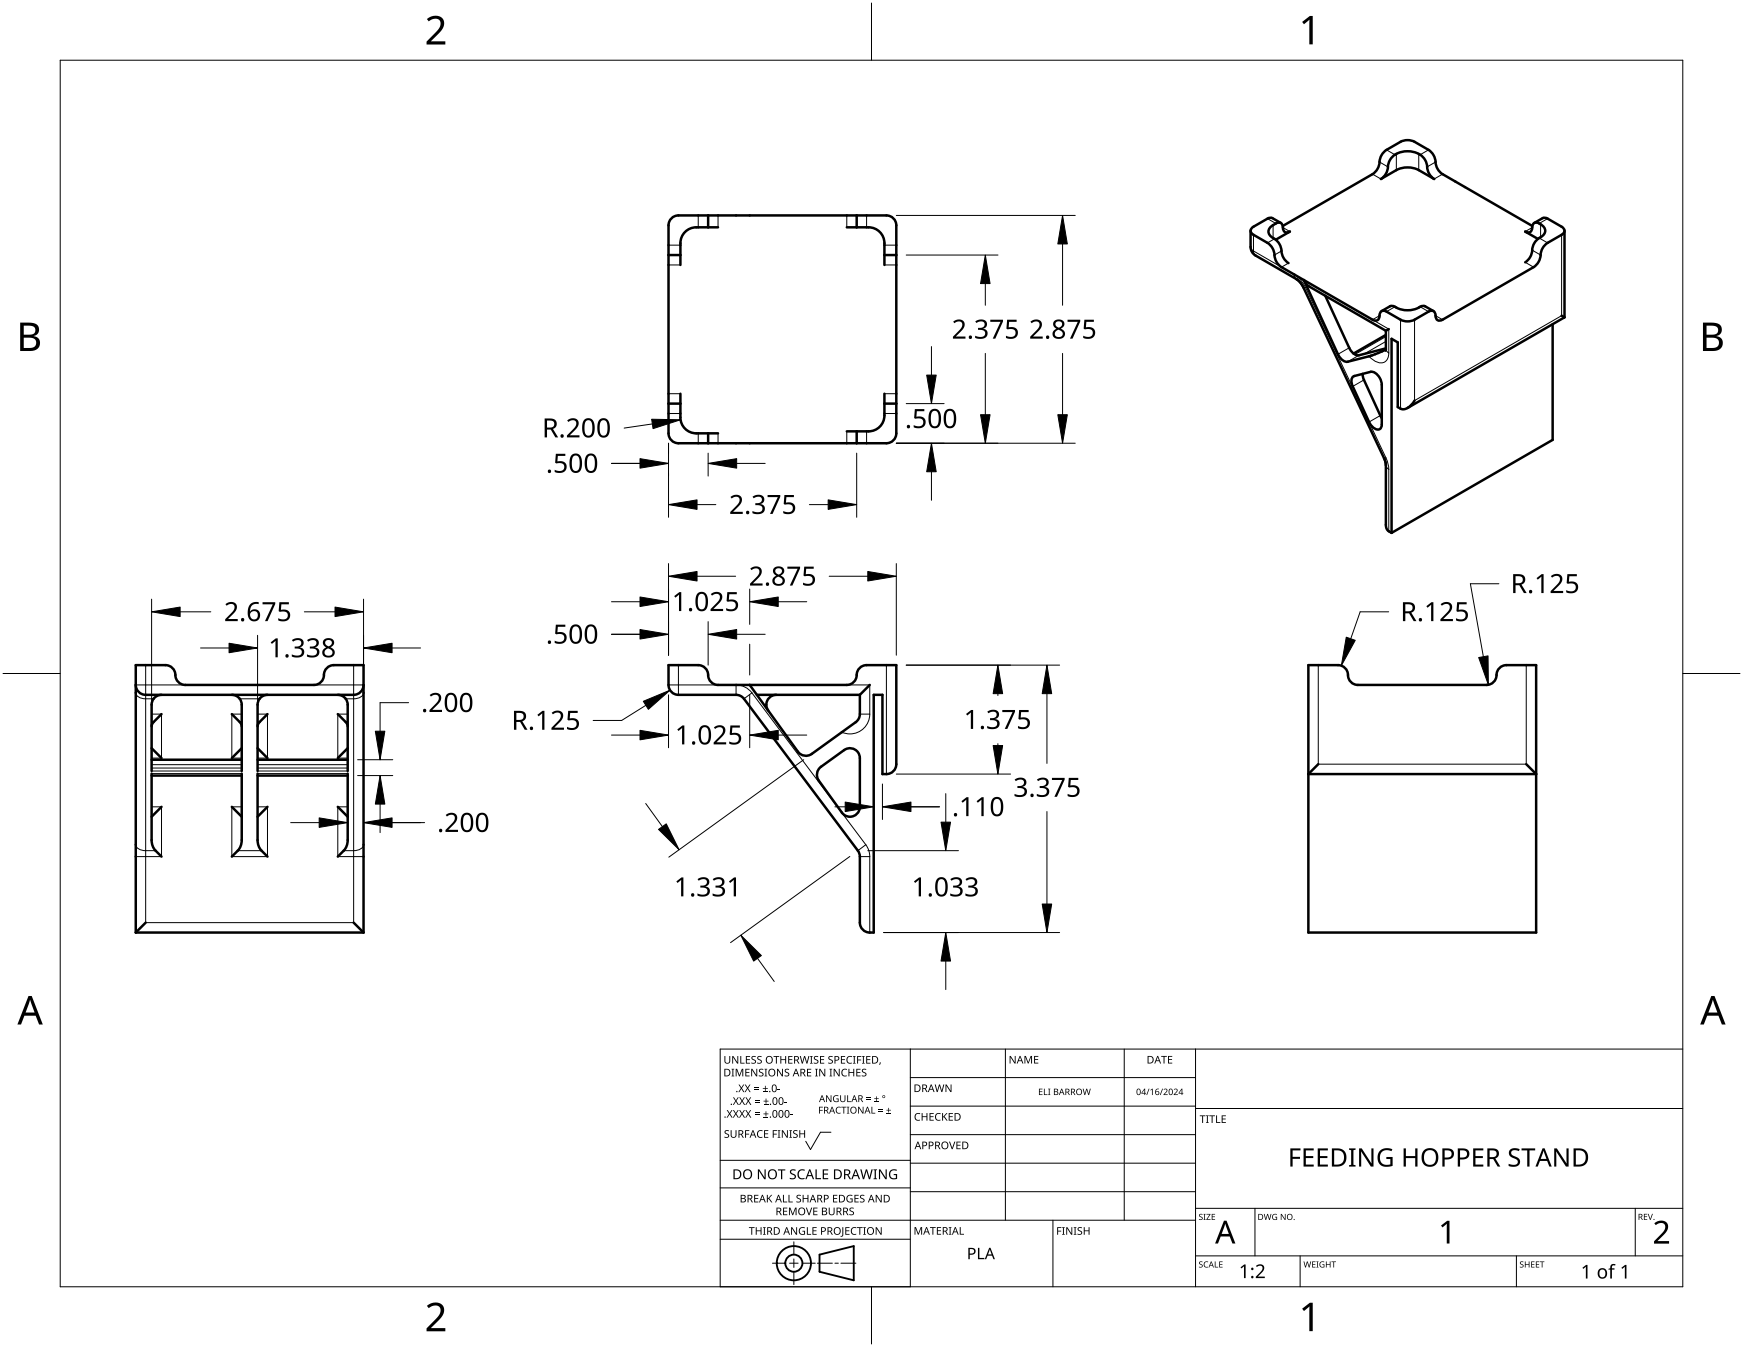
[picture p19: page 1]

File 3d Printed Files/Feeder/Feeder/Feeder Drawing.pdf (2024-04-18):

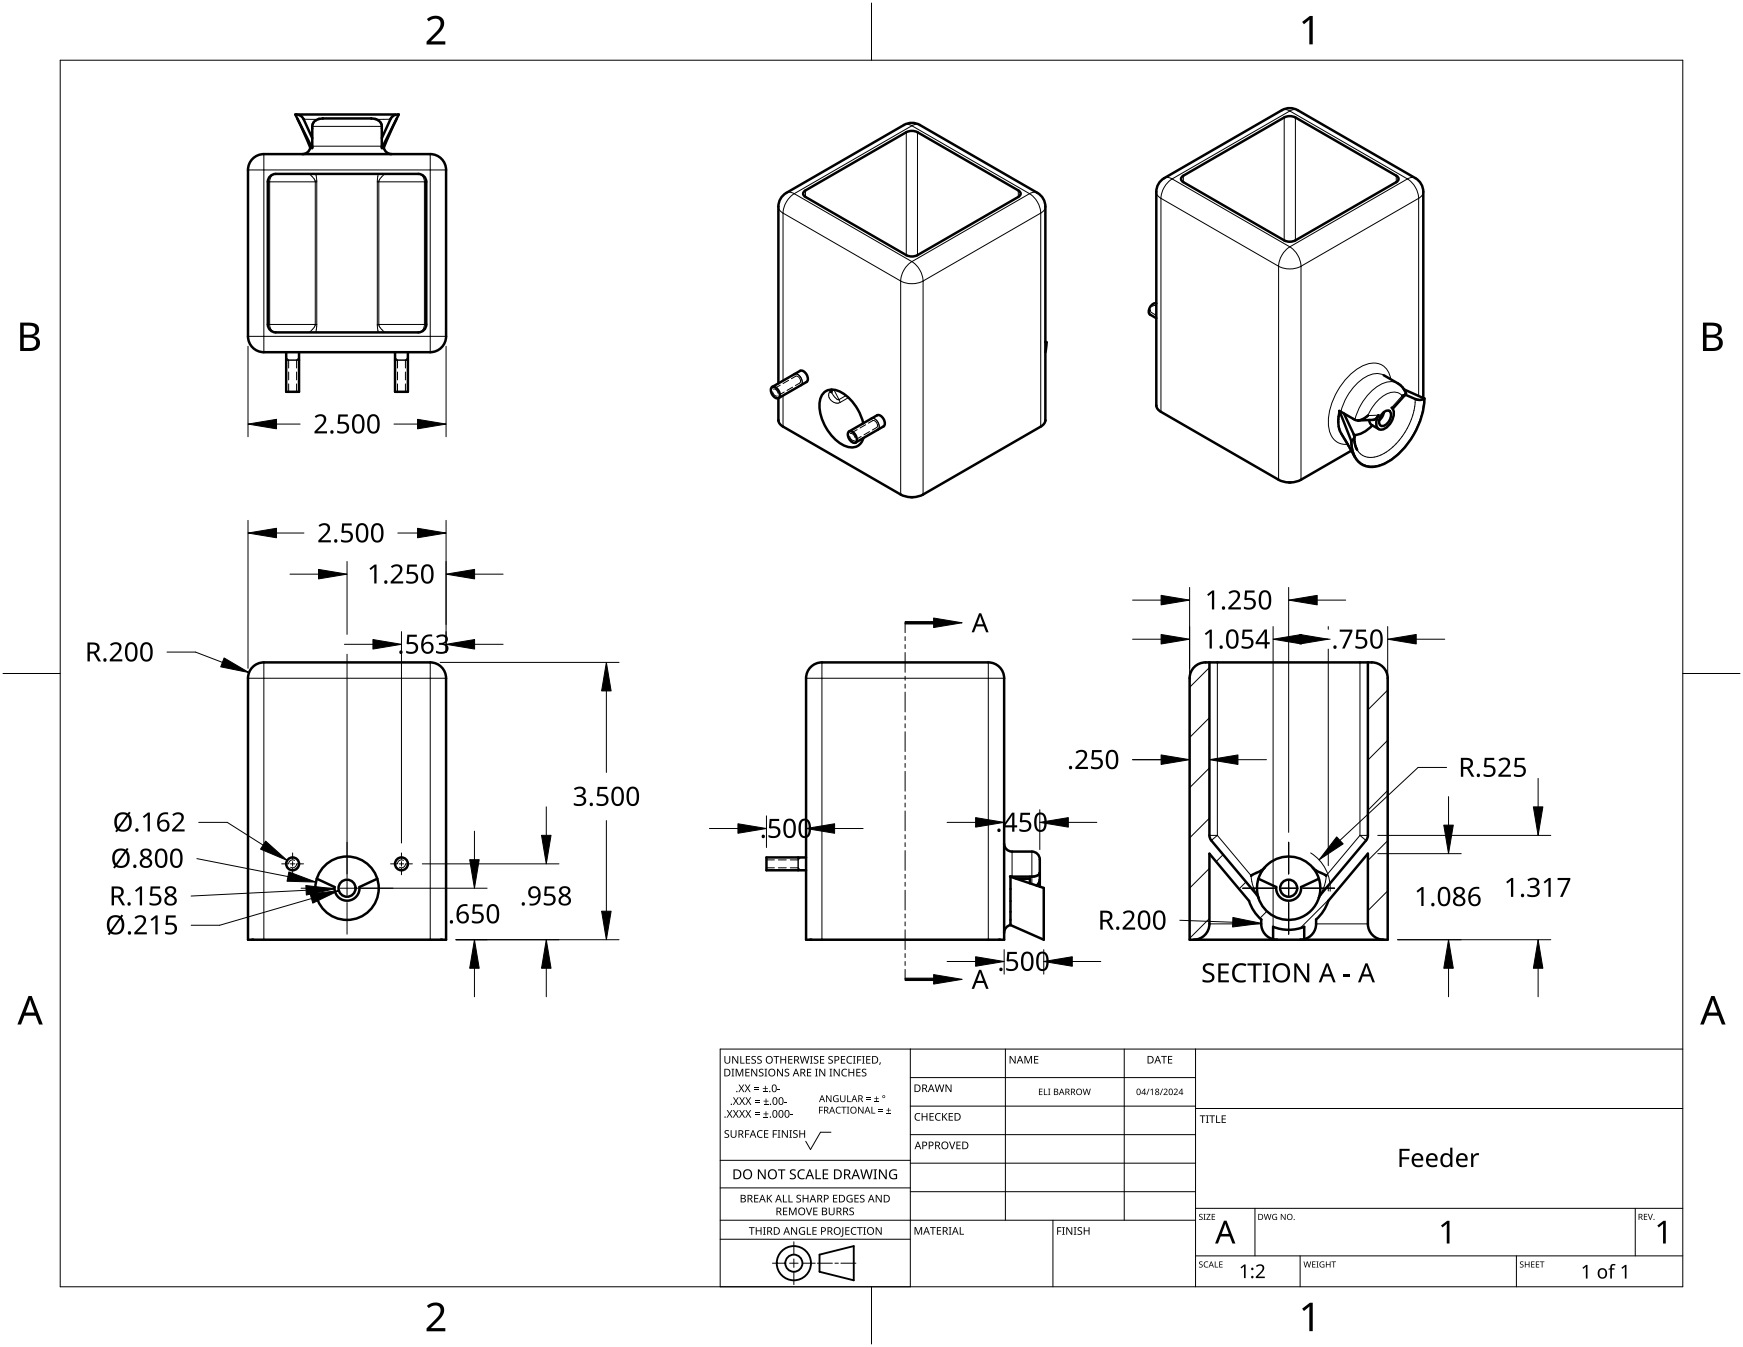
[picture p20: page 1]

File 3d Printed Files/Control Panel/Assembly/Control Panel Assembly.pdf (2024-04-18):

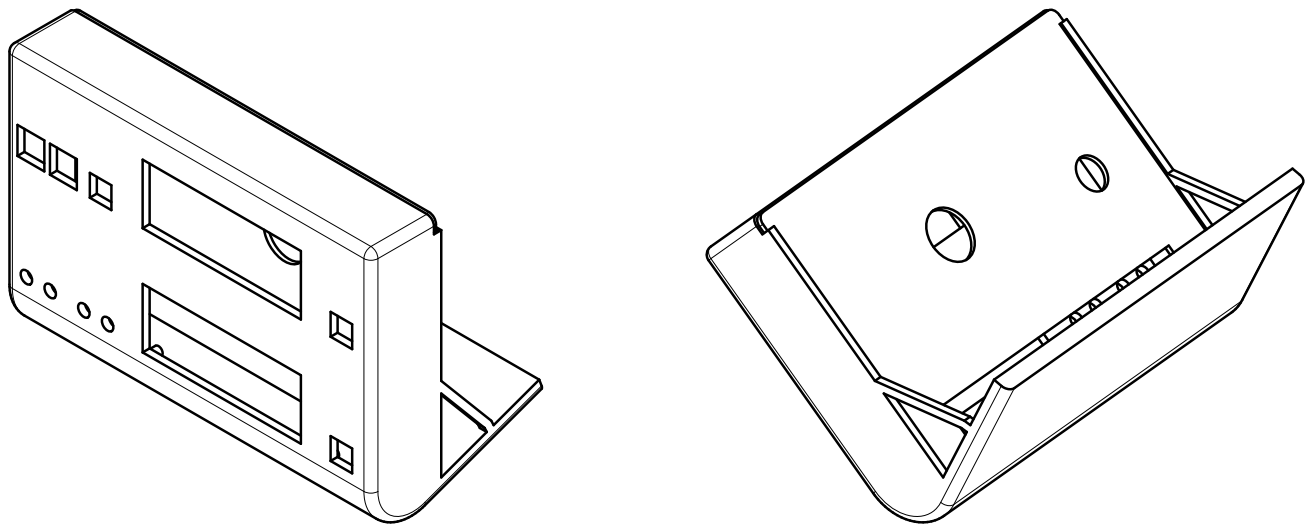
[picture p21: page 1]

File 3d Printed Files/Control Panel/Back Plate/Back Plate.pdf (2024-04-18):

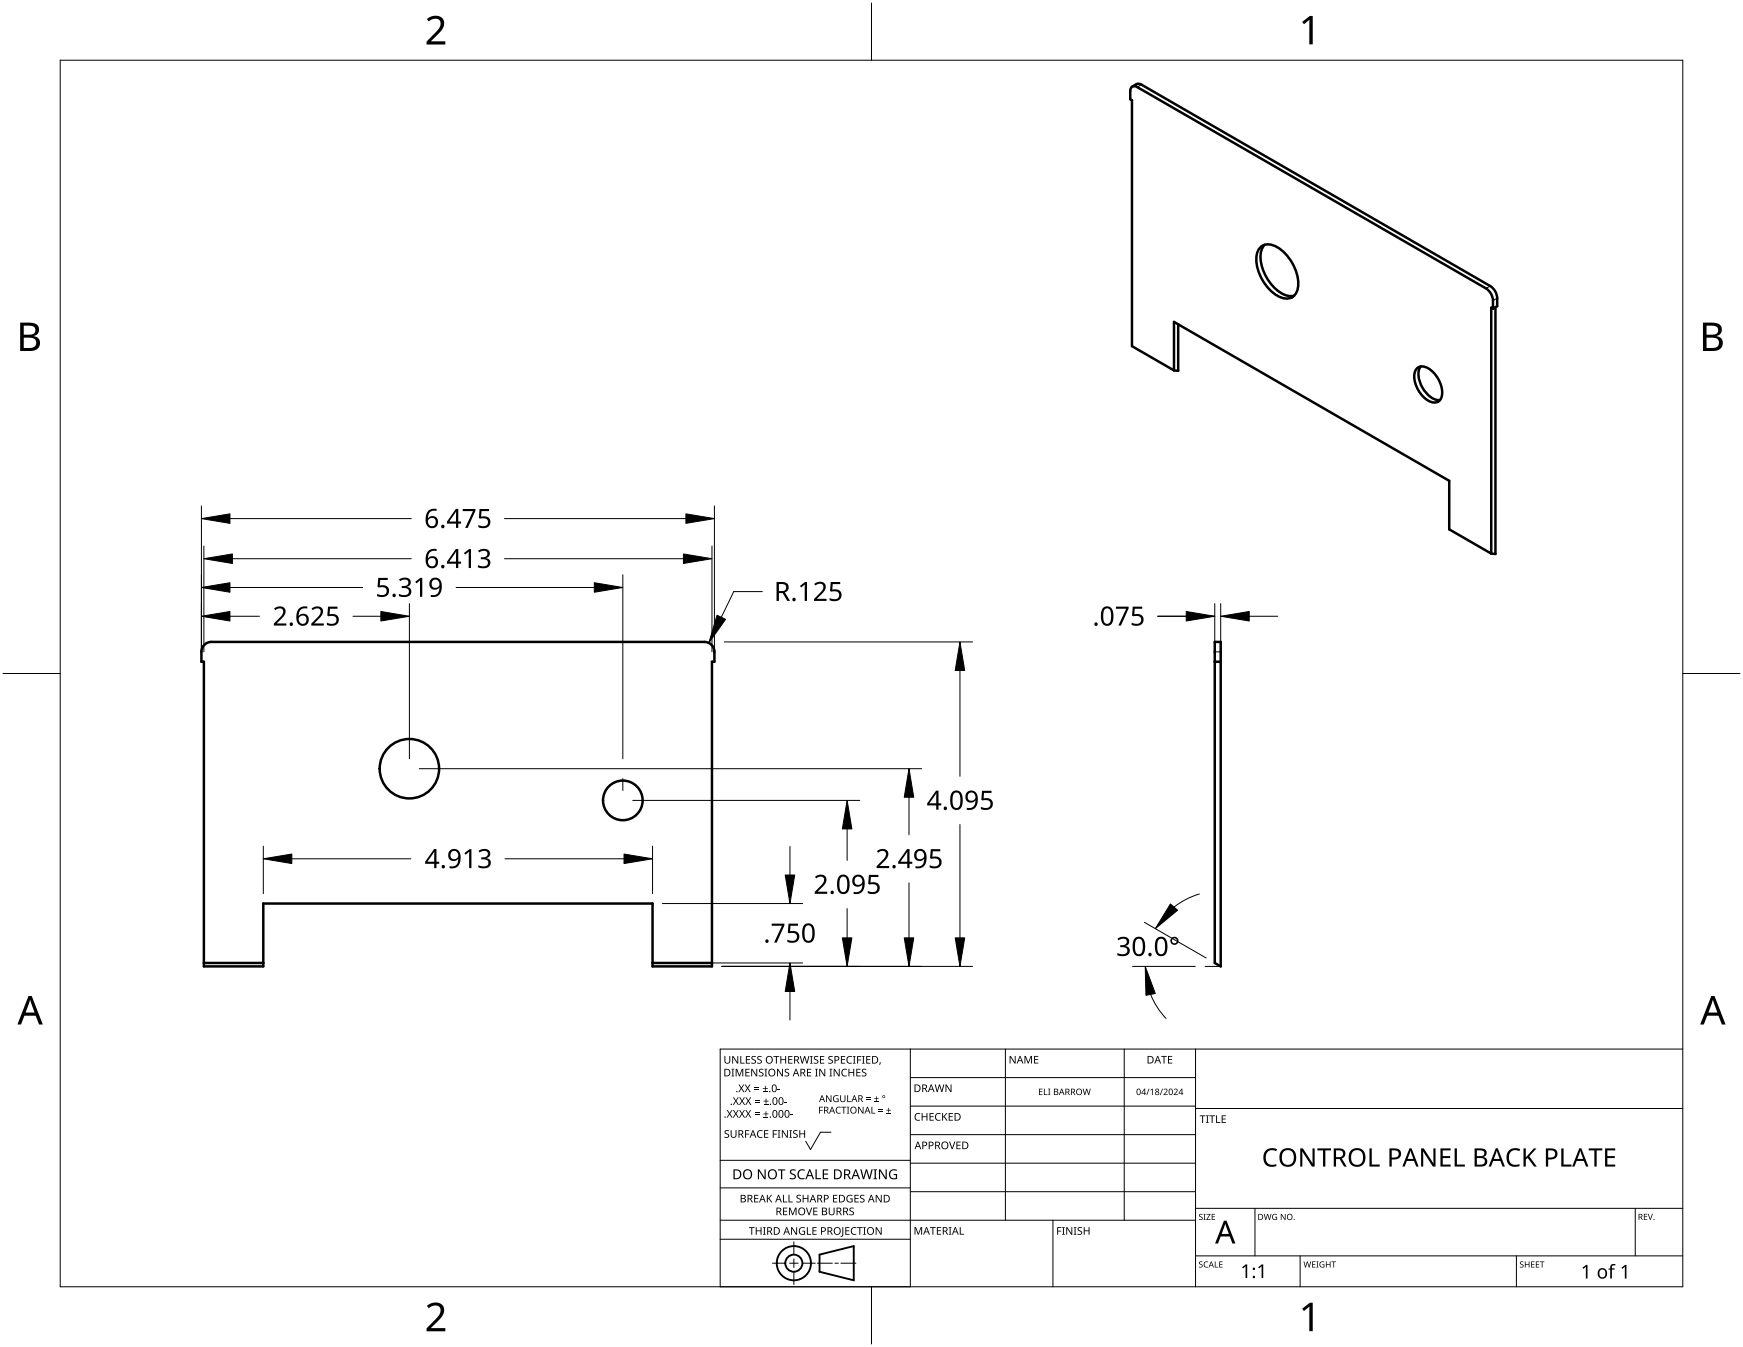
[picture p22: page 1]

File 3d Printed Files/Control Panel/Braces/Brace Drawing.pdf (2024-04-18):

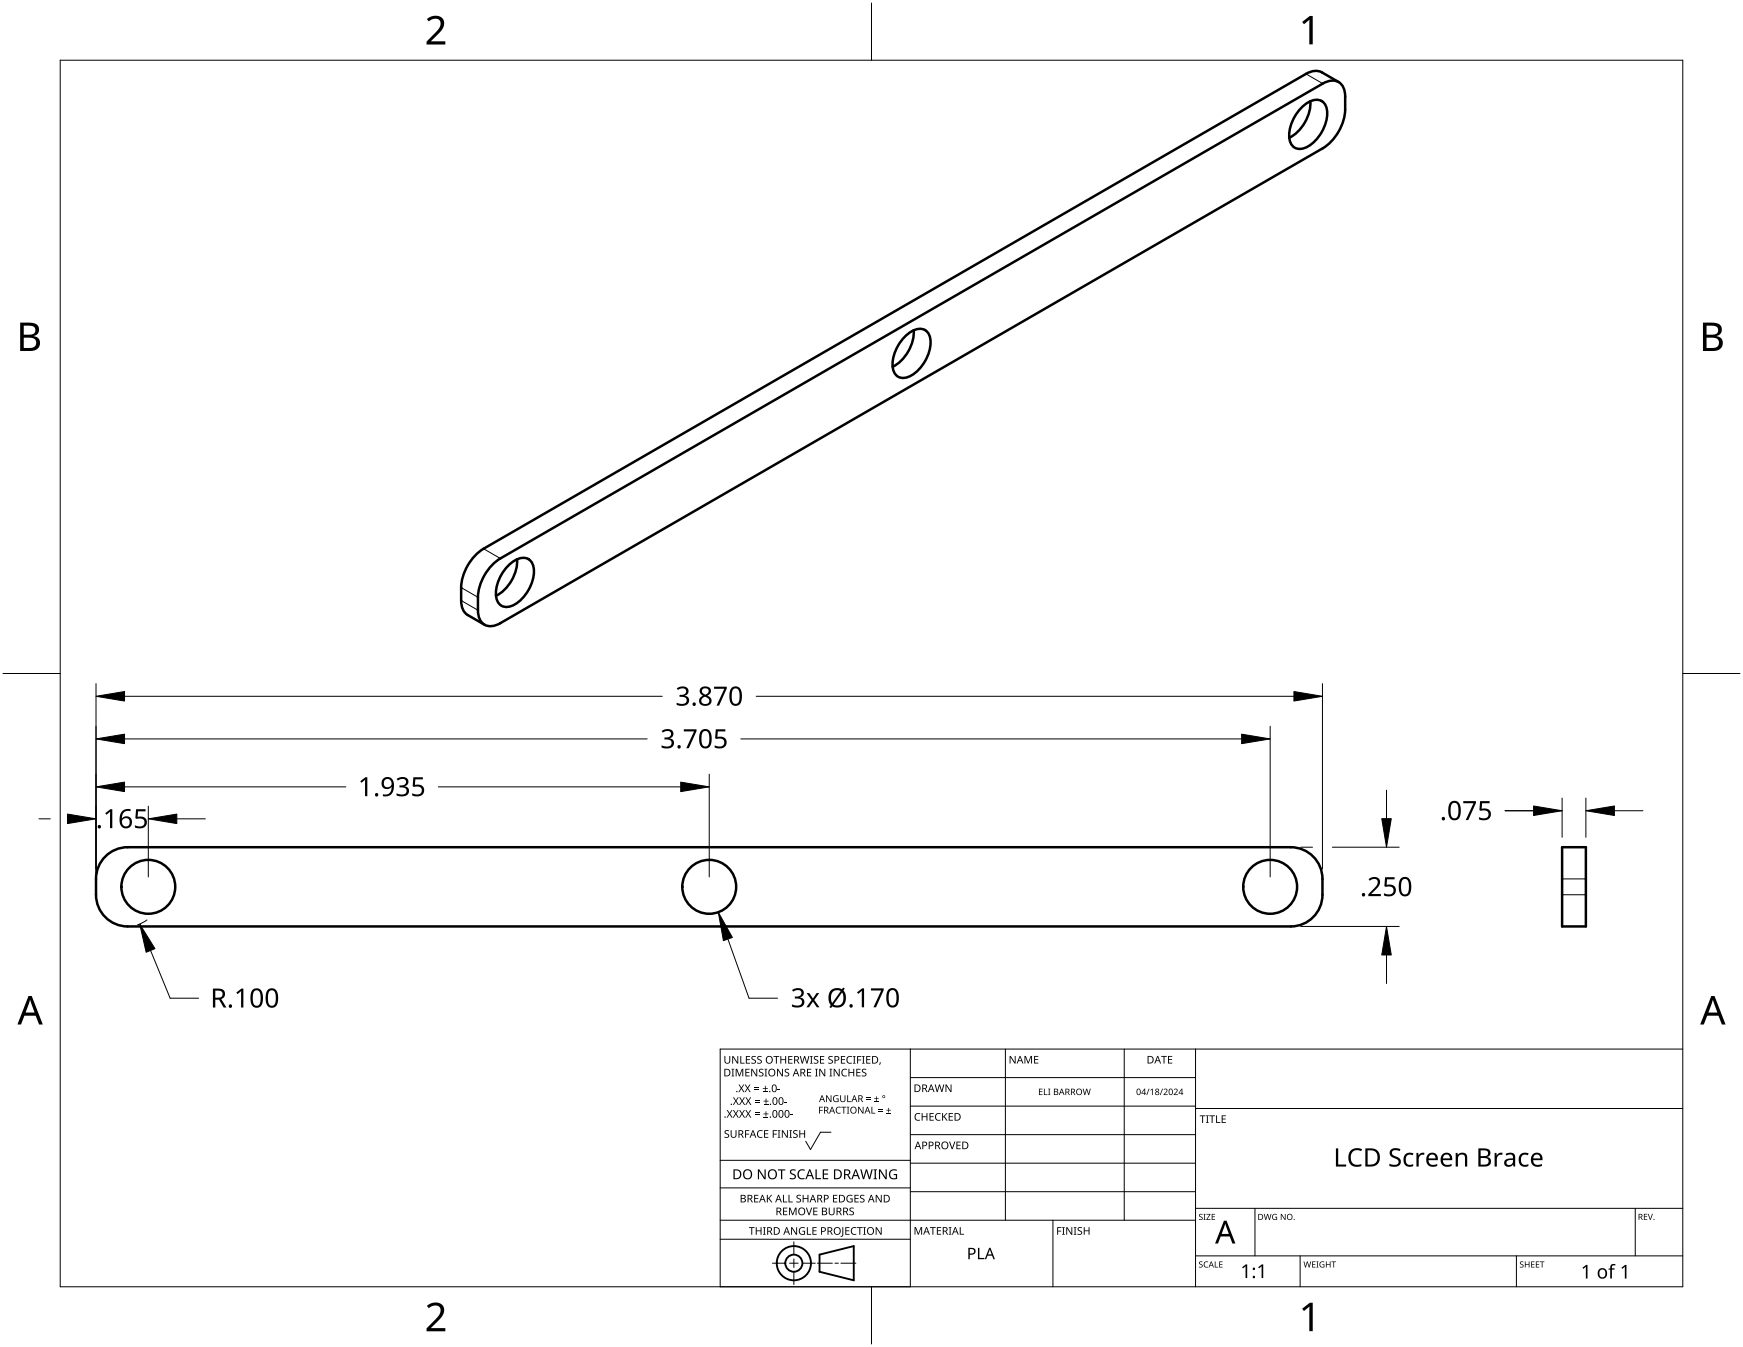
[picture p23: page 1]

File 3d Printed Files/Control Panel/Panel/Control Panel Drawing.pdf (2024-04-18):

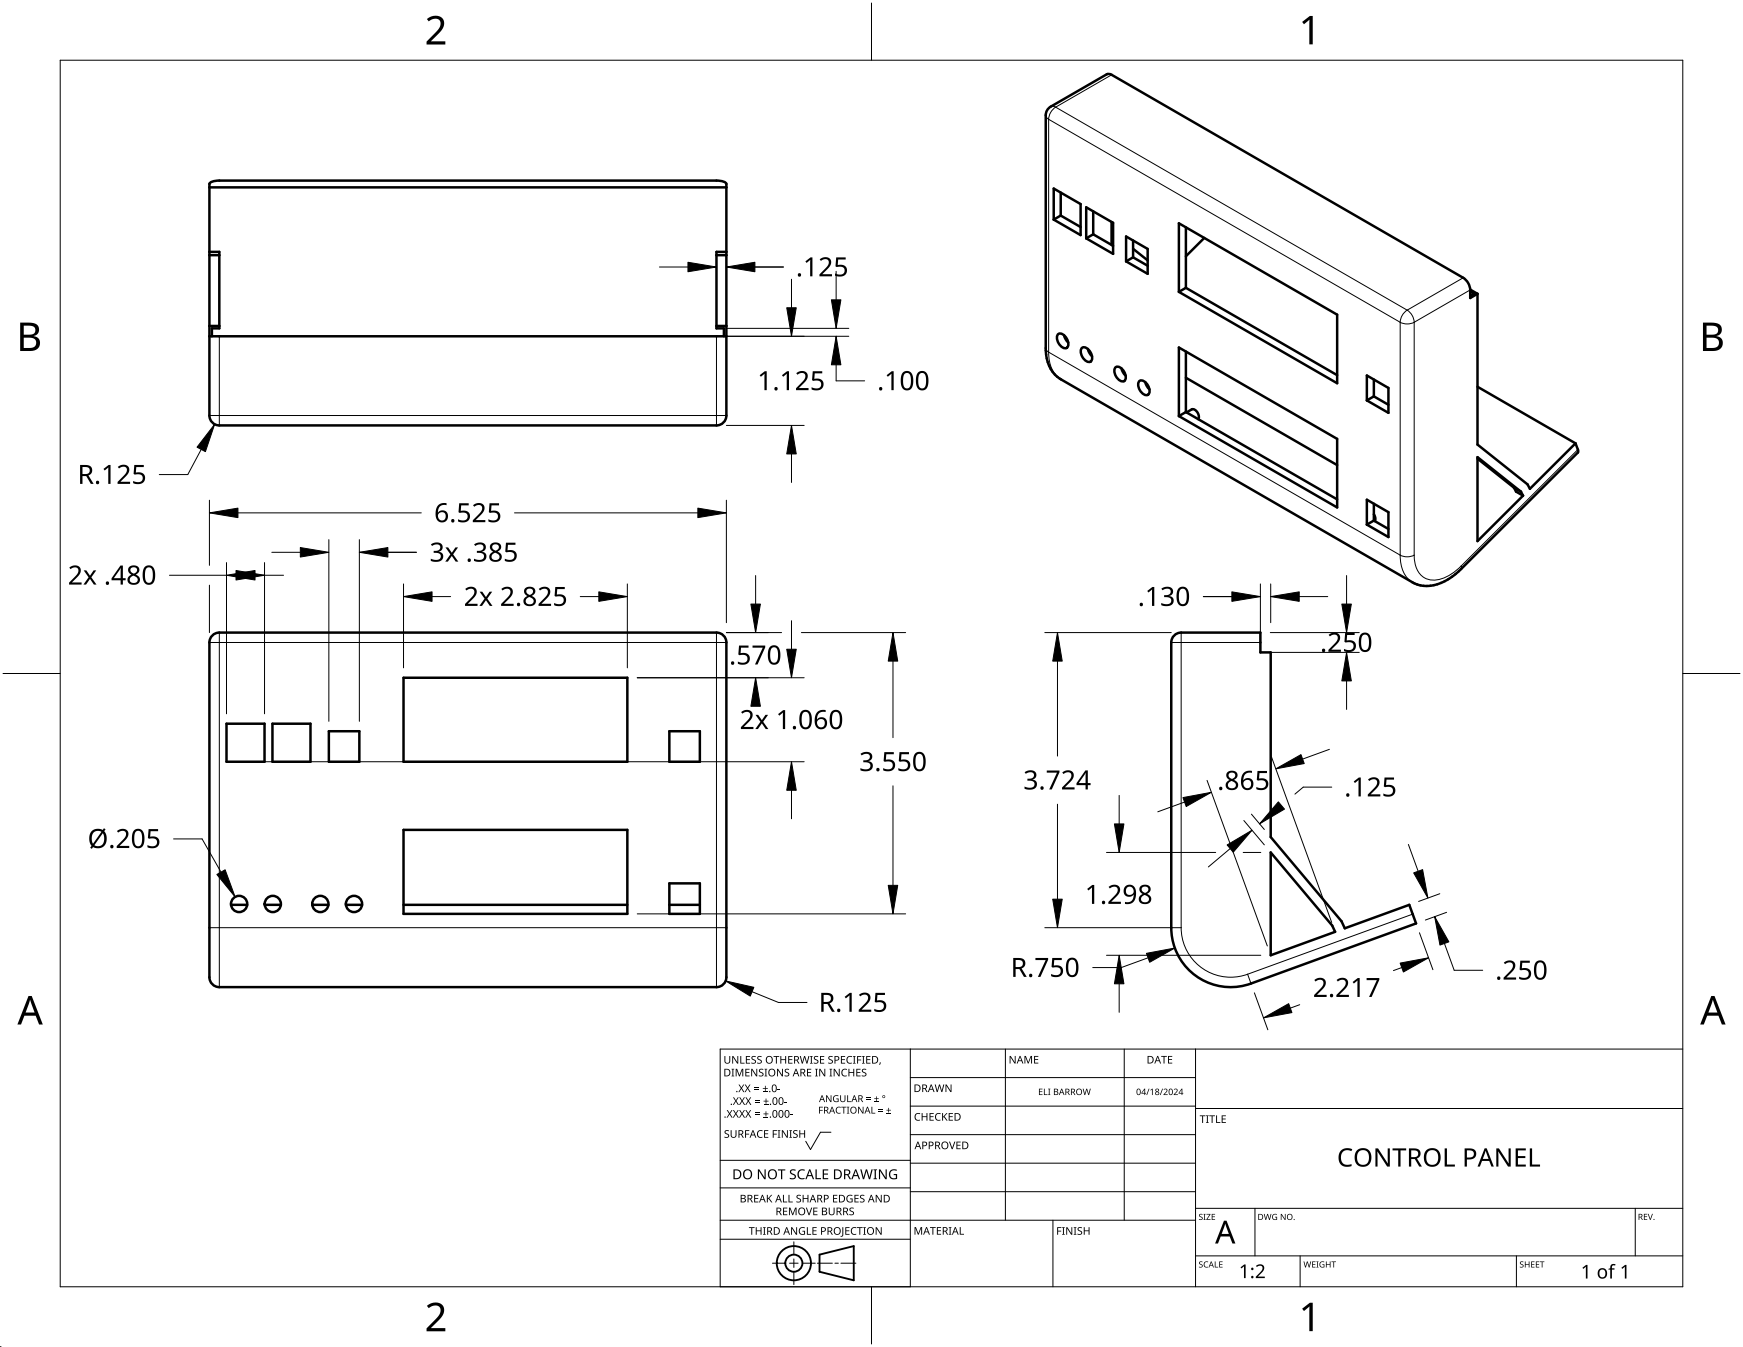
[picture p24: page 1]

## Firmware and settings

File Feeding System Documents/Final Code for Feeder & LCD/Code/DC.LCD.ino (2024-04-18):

#include <LiquidCrystal.h>
#include <Stepper.h>

//Define button and LCD pins
const int buttonPinSet = 7; //Button for setting the feeding interval
const int resetButton = 4; //Button for resetting 
const int rs = 13, en = 12, d4 = 11, d5 = 10, d6 = 9, d7 = 8; //LCD Pins
LiquidCrystal lcd(rs, en, d4, d5, d6, d7); //Adding the LCD screen

// Constants for potentiometer and motor
const int potentiometerPin = A0;  // Potentiometer connected to analog pin A0
const int stepsPerRevolution = 2048; // This is max speed for our stepper motor
Stepper myStepper = Stepper(stepsPerRevolution, 2, 3, 5, 6); //purple is #8 & stepper motor initiation

// Variables
bool motorOn = false; //setting motor status
unsigned long motorStartTime = 0; //Time when motorstarts
unsigned long interval = 0; // Initial interval to zero
int potValue = 0; //initial potentiometer value
bool potentiometerSet = false; //flag for the potentiometer setting



void setup() {
  //set the modes of the pins
  pinMode(buttonPinSet, INPUT_PULLUP);// Set pin for setting interval as input with pull-up
  pinMode(resetButton, INPUT_PULLUP);// Set reset button pin as input with pull-up

    // Initialize the LCD
  lcd.begin(16, 2);  // Initialize the LCD: 16 characters and 2 lines
  lcd.setCursor(0, 0);// Set cursor position to (0, 0)
  lcd.print("Feed Timer   "); // Print initial message on LCD
  Serial.begin(9600); // Initialize serial communication at 9600 baud rate

  
  

}



void loop() {

  //unsigned long firstMillis = millis();

  if (digitalRead(buttonPinSet) == LOW && !potentiometerSet) {
    lcd.clear();// Clear the LCD
    lcd.setCursor(0, 0); // Set cursor to (0, 0)
    lcd.print("Set Feed Timer:   "); // Print message to set feed timer
    lcd.setCursor(0, 1);  // Set cursor to (0, 1)
    lcd.print("                "); // Clear previous message
    
    //lcd.setCursor(0, 1);
    //lcd.print(" ");


    // While button is pressed, read potentiometer and display interval options
    while (digitalRead(buttonPinSet) == LOW) {
      // Read the potentiometer value and display
      potValue = analogRead(potentiometerPin);  // Read potentiometer value
      lcd.setCursor(0, 1); // Set cursor to (0, 1)
      if(potValue >= 0 && potValue <= 255){
        lcd.print("6  Hr Intervals   "); // Print interval option
      } else if (potValue >= 256 && potValue <= 510){
        lcd.print("12 Hr Intervals    ");  // Print interval option
      } else if (potValue >= 511 && potValue <= 765){
        lcd.print("24 Hr Intervals      ");  // Print interval option
      }else if (potValue >= 766 && potValue <= 1023) {
      lcd.print("Test Interval       ");  // Print interval option
    }

      delay(50);  // Small delay for stability
    }

    potentiometerSet = true;  // Set flag to true
    lcd.setCursor(0, 0);  // Set cursor to (0, 0)
    lcd.print("Feeding Schedule   ");  // Print message on LCD
    lcd.setCursor(0, 1);  // Set cursor to (0, 1)
    lcd.print("  Has Been Set    ");  // Print message on LCD
    delay(2000);  // Delay for stability
    
  }



  // Map the potentiometer value to the interval range

  if (potentiometerSet) {
    if (potValue >= 0 && potValue <= 255) {
      interval = 21600000; // 6 hours in millis
    }   else if (potValue >= 256 && potValue <= 510) {
      interval = 43200000; // 12 hours in millis
    }   else if (potValue >= 511 && potValue <= 765) {
      interval = 86400000; // 86400000 for 24 hours
    } else if (potValue >= 766 && potValue <= 1023) {
      interval = 10000; // 86400000 for 24 hours
    }
  
    //Serial.println(interval);  // Print interval to serial monitor
    delay(700);
  // If the potentiometer is turned, turn on motor
   if (potValue != 0 && !motorOn ) {
     motorOn = true;  // Set motor status to on
     motorStartTime = millis();  // Record motor start time
     lcd.clear();  // Clear the LCD
     lcd.setCursor(0, 0);  // Set cursor to (0, 0)
     lcd.print("Auger ON");  // Print "Auger ON" message on LCD

     delay(100);


      
   }
  
  // If motor is on, calculate time remaining and display on LCD
   if (motorOn) {
     unsigned long currentMillis = millis(); // Get current time
      unsigned long motorElapsedTime =0; // Motor elapsed time

       // Run the motor for 3 (however long is needed) seconds
        while (motorElapsedTime < 3000) {
          myStepper.setSpeed(10); // Set motor speed
          myStepper.step(1); // Move one step
          delay(10); // Adjust delay for desired speed
          motorElapsedTime = motorElapsedTime +10; // Increment elapsed time
        }
             delay(100);
            motorElapsedTime = 3100; // Reset motor elapsed time for next cycle
            delay(100);

     if (motorElapsedTime > 3000) {
        delay(100);
       lcd.clear(); // Clear the LCD
       delay(100);
       lcd.setCursor(0, 0); // Set cursor to (0, 0)
       delay(100);
       lcd.print("Auger OFF"); // Set cursor to (0, 0)
       delay(1000); // Small delay for stability


        unsigned long newcurrentMillis = millis(); // Get current time

      int remainingTime =0; //Remaining Time


      // Calculate remaining time and display on LCD
      while(remainingTime<=0){
        unsigned long elapsedTime = millis() - newcurrentMillis; // Calculate elapsed time
        delay(100);

        unsigned long remainingTime = interval - elapsedTime; // Calculate remaining time
          
         // Serial.println(remainingTime); // Print remaining time to serial monitor
        int hours = remainingTime / (3600000); // Calculate hours
        //Serial.println("hours is ");
        //Serial.println(hours);

        int minutes = (remainingTime % (3600000)) / (60000); // Calculate mins
        //Serial.println("mins is ");
        //Serial.println(minutes);

        int seconds = (remainingTime % (60000)) / 1000; // Calculate seconds
        //Serial.println("sec is ");
        //Serial.println(seconds);

       lcd.setCursor(0, 1);    // Calculate hours
       lcd.print("Time: ");    // Print "Time:" message on LCD
       lcd.print(hours);       // Print hours on LCD
       delay(10);              // Small delay for stability
       lcd.print("h ");        // Print "h" on LCD
       lcd.print(minutes);     // Print minutes on LCD
       delay(10);              // Small delay for stability
       lcd.print("m ");        // Print "m" on LCD 
       lcd.print(seconds);     // Print seconds on LCD
       delay(10);              // Small delay for stability
       lcd.print("s ");        //Print "s" on LCD 
       delay(10);              // Small delay for stability


        // Reset all variables and flags if reset button is pressed
       if (digitalRead(resetButton) == HIGH) {
         // Reset all variables and flags
        motorOn = false;
        potentiometerSet = false;
        interval = 0;
        potValue = 0;
    
        lcd.clear(); // Clear the LCD
        lcd.setCursor(0, 0); // Set cursor to (0, 0)
        lcd.print("Resetting...    "); // Print "Resetting..." message on LCD
        delay(1000); // Delay for stability
    
        // Re-initialize the LCD display
        lcd.clear();
        lcd.setCursor(0, 0);
          }


          // Break loop if interval is greater than 864,000,000 milliseconds (24 hours)
          if (remainingTime > 864000000){
            lcd.setCursor(0, 0); // Set cursor to (0, 0)
            lcd.print("Auger ON         "); // Print "Auger ON" message on LCD
            delay(10); // Small delay for stability
            lcd.setCursor(0, 1); // Set cursor to (0, 1)
            lcd.print("Feeding Occuring"); // Print "Feeding Occuring" message on LCD
            break; // Exit the loop
          }
          delay(700); // Small delay for stability
        }
       }
     }  
    }
  }



  

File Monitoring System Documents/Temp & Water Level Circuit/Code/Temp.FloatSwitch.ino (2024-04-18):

#include <LiquidCrystal.h>



//const int PushButton = 4; //Pushbutton on pin 4
int value = 0; // variable reading for the pushbutton.

// Below this line is for the Thermistor Readings

int ThermistorPin = 0;
int Vo;
float R1 = 10000;
float logR2, R2, T, Tc;
float c1 = 1.009249522e-03, c2 = 2.378405444e-04, c3 = 2.019202697e-07;

LiquidCrystal lcd(13, 12, 11, 10, 9, 8);
//initializing variables to be used.
int TempGreenLed=7;
int TempRedLed = 6;
int FloatSwitch = 5;
int LevelGreenLed = 4;
int LevelRedLed = 3;
int buttonState =1;


void setup() {
  // put your setup code here, to run once:
  //Setting pin modes for the LED's buttons and thermistor
  pinMode(TempGreenLed, OUTPUT);
  pinMode(TempRedLed, OUTPUT);
  pinMode (ThermistorPin, OUTPUT); 
  pinMode(FloatSwitch, INPUT_PULLUP);
  pinMode(LevelGreenLed, OUTPUT);
  pinMode(LevelRedLed, OUTPUT);
  //pinMode (PushButton, INPUT);
  
 lcd.begin(16, 2);  // Initialize the LCD: 16 characters and 2 lines
  lcd.setCursor(0, 0);// Set cursor position to (0, 0)
  //lcd.print("Feed Timer   "); // Print initial message on LCD
  //Serial.begin(9600);
  //delay(2000);
  

 
}

void loop() {
      //Reading value of thermistor to calculate the temps.
        Vo = analogRead(ThermistorPin);
        R2 = R1 * (1023.0 / (float)Vo - 1.0);
        logR2 = log(R2);
        T = (1.0 / (c1 + c2*logR2 + c3*logR2*logR2*logR2));
        Tc = T - 273.15; //Temp in Celsius
        T = (Tc * 9.0)/ 5.0 + 32.0; //Temp in F

        if (T > 90 || T < 75){ //Here is where we set desired temperature for the water
          digitalWrite(TempRedLed, HIGH); //if out of range, red light turns on
          digitalWrite(TempGreenLed, LOW); //if out of range, green light turns off
        } else {
          digitalWrite(TempRedLed, LOW); //if in  range, red light turns off
          digitalWrite(TempGreenLed, HIGH); //if in range, green light turns on

        }
        //Serial.print("Temperature: "); 
        //Serial.print(T);
        //Serial.println(" F"); 

        lcd.setCursor(0, 0);// Set cursor position to (0, 0)
        lcd.print("   Water Temp");

        lcd.setCursor(0, 1); //printing the temp in F to screen
        lcd.print(T);
        lcd.print(" F ");

        lcd.setCursor(8, 1); //printing the temp in C to screen
        lcd.print(" ");
        lcd.print(Tc);
        lcd.print(" C");

        delay(5000);

        lcd.setCursor(0, 0);   //Clearing off Screen for next message
        lcd.print("                     ");
        lcd.setCursor(0, 1);
        lcd.print("                   ");

        buttonState= digitalRead(FloatSwitch);
        if (buttonState == LOW){ 
          digitalWrite(LevelRedLed, HIGH); //if button not pressed, red light turns on
          digitalWrite(LevelGreenLed, LOW); //if button not pressed, green light turns off
          lcd.setCursor(0, 0);
          lcd.print("  Water Level"); //Printing water updates
          lcd.setCursor(0, 1);
          lcd.print(" LOW: ADD WATER");
          delay(5000);
          } else {
            digitalWrite(LevelGreenLed, HIGH); //if button pressed , green light turns on
            digitalWrite(LevelRedLed, LOW); //if button pressed, red light turns off
            lcd.setCursor(0, 0);
            lcd.print("  Water Level"); //Printing water updates
            lcd.setCursor(0, 1);
            lcd.print( "     Good ");
            delay(5000);
            }
      }





      
